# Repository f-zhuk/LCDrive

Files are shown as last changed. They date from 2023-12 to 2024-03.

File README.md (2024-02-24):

# LCDrive
This project shows what happens if you take an ordinary cycloidal reducer and unfold it into a straight line
Well, not so straight actually

The actuator is made out of four plates, two of which are guiding plates for alignment and two are pushing sliders.
In this device, sliders travel in circles with a radius of 1mm relative to the alignment plate. Sliders are 180 degrees out of phase.
Travel trajectory is defined by eccentrics mounted on shafts of two motors that run synchronously.
All plates have slots. Sliders have cycloidal cutouts, alignments have linear path cutouts. 

Now let’s add the carriage. All cutouts have a width equal to pin's diameter. The pin is ideally an integral part of the carriage and it engages with the edges of the cutouts. Cutouts in all plates define the exact position of the pin at every moment in time.

Pin and carriage respectively are pushed along the axis with the motors rotation.

In full-step mode, it takes 32 steps for one revolution of the internal shaft, 63.68 turns of the internal shaft for the single main shaft revolution, and 1.59 main shaft revolutions to slide the carriage from start to finish, or 3240 steps in total. 

In the ideal world, it is approximately 3.1 micrometers of linear movement per step.

Since I am not satisfied with current situation with parametric curves and offset tools in FreeCAD I wrote a small Python script to generate SVGs for import. Extruded pads I have prototyped with FDM which took me a couple of iterations. Then I milled my parts with a 1mm endmill out of 2mm aluminum strip. Using FreeCAD as a CAM has its drawbacks and at this point I think it might be reasonable to generate G-code in the same Python script skipping the FreeCAD part.

Advantages: 

1. No screw drive
2. Slim design
3. Great step distance

Disadvantages:

1. Large backlash
2. High resistance resulting in low pushing force

Possible improvements:

1. Add one more phase to get a 120-degree difference between moving slides
2. Add miniature bearings
3. Motor synchronization and feedback

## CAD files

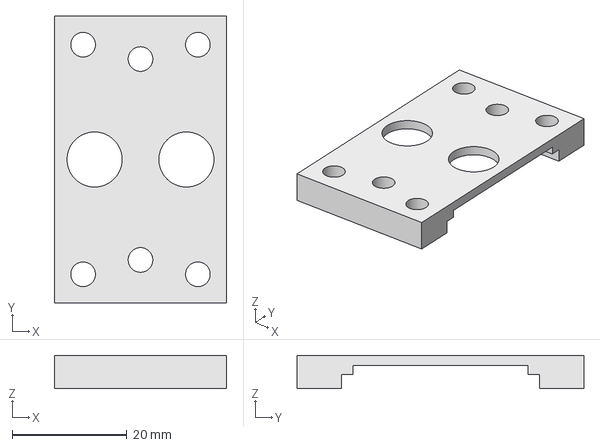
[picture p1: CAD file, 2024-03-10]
Mechanical/motor_top-motor_top.step
30.0 x 50.0 x 5.80 mm
LCS_0
motor_top001

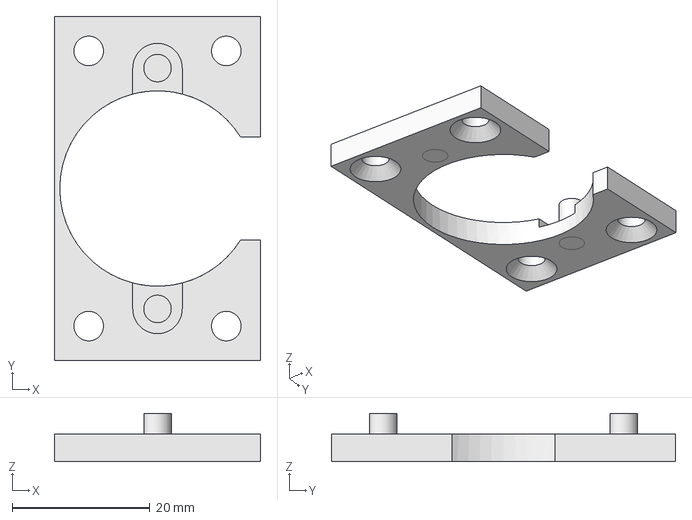
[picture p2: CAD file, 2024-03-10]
Mechanical/motor_bot-motor_bot.step
30.0 x 50.0 x 7.00 mm
LCS_0
motor_bot001

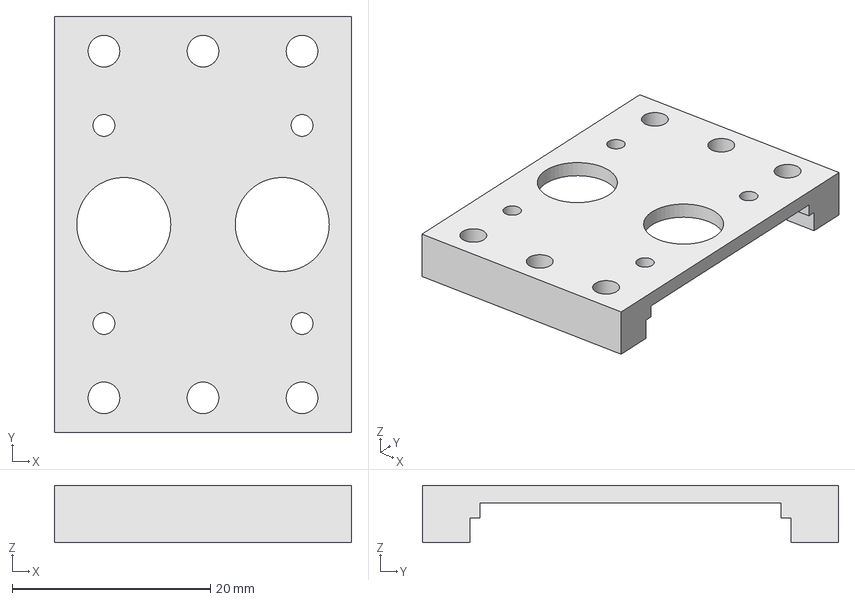
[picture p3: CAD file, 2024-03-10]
Mechanical/carriage_top-carriage_top.step
30.0 x 42.0 x 5.80 mm
LCS_0
carriage_top001

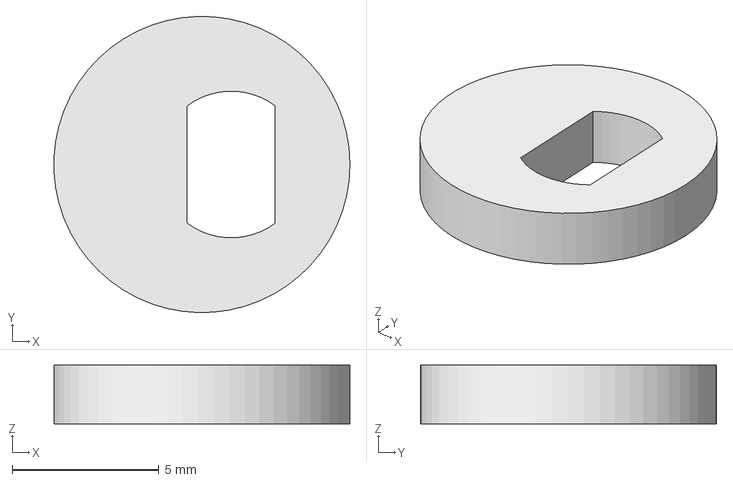
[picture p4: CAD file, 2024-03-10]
Mechanical/eccentric-eccentric.step
10.1 x 10.1 x 2.00 mm
LCS_0
eccentric001

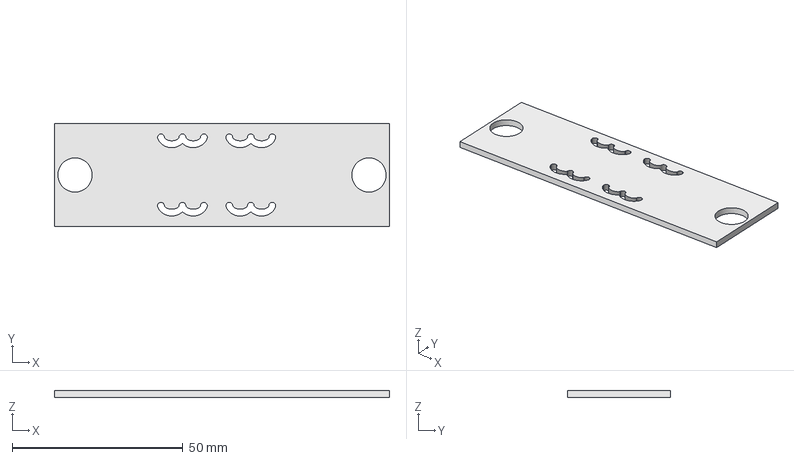
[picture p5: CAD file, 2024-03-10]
Mechanical/slot-slot.step
98.0 x 30.0 x 2.00 mm
LCS_0
slot001

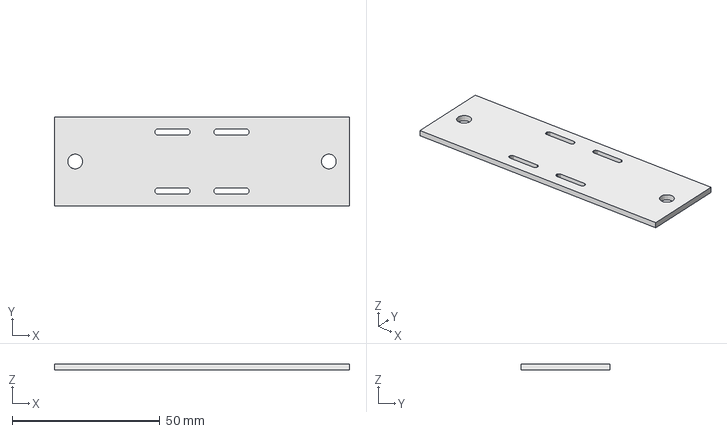
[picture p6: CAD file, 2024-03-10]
Mechanical/base-base.step
100.0 x 30.0 x 2.00 mm
LCS_0
base001

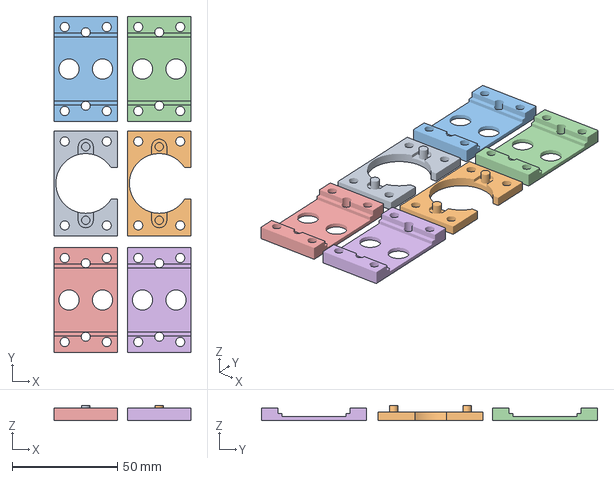
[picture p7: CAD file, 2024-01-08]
Mechanical/motor_case.3mf
65.0 x 160.0 x 7.00 mm
motor_bot-motor_bot.stl x 2
motor_top-motor_top.stl x 4

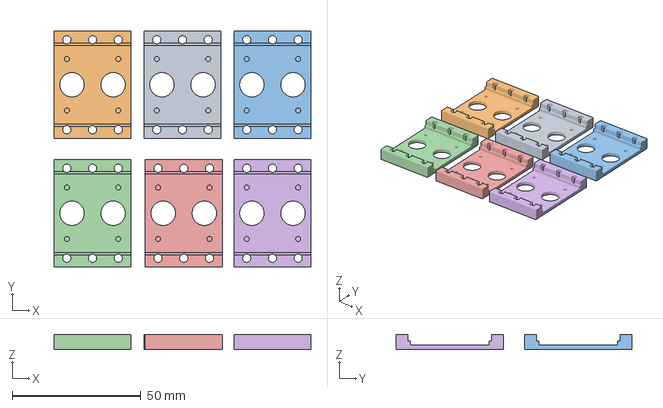
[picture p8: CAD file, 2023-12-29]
Mechanical/carriage_top-carriage_topcarriage_top001.3mf
100.0 x 92.0 x 5.80 mm
carriage_top-carriage_topcarriage_top001.stl x 6

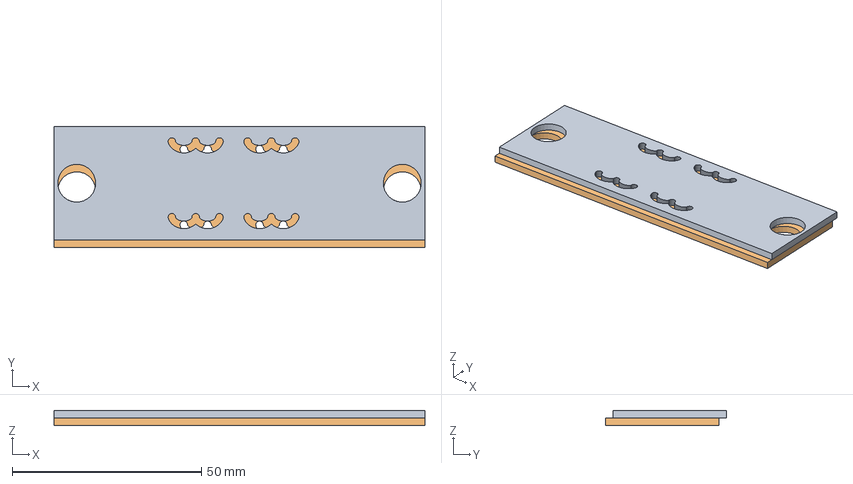
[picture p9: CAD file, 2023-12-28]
Mechanical/slot.FCStd
98.0 x 32.0 x 4.00 mm
slot001
slot002

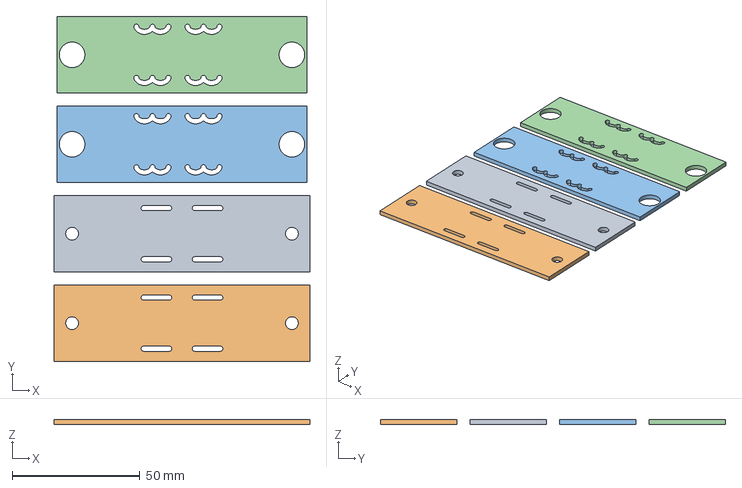
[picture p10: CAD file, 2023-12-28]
Mechanical/base-basebase001.3mf
100.0 x 135.0 x 2.00 mm
base-basebase001.stl x 2
slot-slotslot001.stl x 2

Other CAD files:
Mechanical/motor_top.FCStd
Mechanical/motor_bot.FCStd
Mechanical/eccentric.FCStd
Mechanical/slot_mill.FCStd
Mechanical/carriage_top.FCStd
Mechanical/base_mill.FCStd
Mechanical/slot-slotslot001.stl
Mechanical/base.FCStd
Mechanical/base-basebase001.stl
Mechanical/carriage_top-carriage_topcarriage_top001.stl
Mechanical/eccentric-eccentric.3mf
Mechanical/eccentric-eccentric.stl
Mechanical/motor_bot-motor_bot.stl
Mechanical/motor_top-motor_top.stl

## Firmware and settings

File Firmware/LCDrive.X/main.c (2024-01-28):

/**
  Generated Main Source File

  Company:
    Microchip Technology Inc.

  File Name:
    main.c

  Summary:
    This is the main file generated using PIC10 / PIC12 / PIC16 / PIC18 MCUs

  Description:
    This header file provides implementations for driver APIs for all modules selected in the GUI.
    Generation Information :
        Product Revision  :  PIC10 / PIC12 / PIC16 / PIC18 MCUs - 1.81.8
        Device            :  PIC18F26K83
        Driver Version    :  2.00
*/

/*
    (c) 2018 Microchip Technology Inc. and its subsidiaries. 
    
    Subject to your compliance with these terms, you may use Microchip software and any 
    derivatives exclusively with Microchip products. It is your responsibility to comply with third party 
    license terms applicable to your use of third party software (including open source software) that 
    may accompany Microchip software.
    
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
    IN NO EVENT WILL MICROCHIP BE LIABLE FOR ANY INDIRECT, SPECIAL, PUNITIVE, 
    INCIDENTAL OR CONSEQUENTIAL LOSS, DAMAGE, COST OR EXPENSE OF ANY KIND 
    WHATSOEVER RELATED TO THE SOFTWARE, HOWEVER CAUSED, EVEN IF MICROCHIP 
    HAS BEEN ADVISED OF THE POSSIBILITY OR THE DAMAGES ARE FORESEEABLE. TO 
    THE FULLEST EXTENT ALLOWED BY LAW, MICROCHIP'S TOTAL LIABILITY ON ALL 
    CLAIMS IN ANY WAY RELATED TO THIS SOFTWARE WILL NOT EXCEED THE AMOUNT 
    OF FEES, IF ANY, THAT YOU HAVE PAID DIRECTLY TO MICROCHIP FOR THIS 
    SOFTWARE.
*/

#include "mcc_generated_files/mcc.h"

void TMR0_stepISR()
{
    static uint16_t step = 0;
    step ++;
    if(step == 3500) 
    {
        DMA1CON1 = (DMA1CON1&~0x06)|0x04;
        DMA1SSA = (&SrcVarName0)+8;
    }
    if(step > 7000) 
    {
        step = 0;
        DMA1CON1 = (DMA1CON1&~0x06)|0x02;
        DMA1SSA = &SrcVarName0;
    }
}

/*
                         Main application
 */
void main(void)
{
    // Initialize the device
    SYSTEM_Initialize();
    
    TMR0_SetInterruptHandler (TMR0_stepISR);
    
    SrcVarName0[0] = 0x09;
    SrcVarName0[1] = 0x0C;
    SrcVarName0[2] = 0x06;
    SrcVarName0[3] = 0x03;
    SrcVarName0[4] = 0x09;
    SrcVarName0[5] = 0x0C;
    SrcVarName0[6] = 0x06;
    SrcVarName0[7] = 0x03;
    //SrcVarName0[0] = 0x09;
    //SrcVarName0[1] = 0x05;
    //SrcVarName0[2] = 0x06;
    //SrcVarName0[3] = 0x0A;
    //SrcVarName0[4] = 0x09;
    //SrcVarName0[5] = 0x05;
    //SrcVarName0[6] = 0x06;
    //SrcVarName0[7] = 0x0A;
    DMA1DSA= (volatile unsigned short)&PORTC; //DMA1 destination address

    // If using interrupts in PIC18 High/Low Priority Mode you need to enable the Global High and Low Interrupts
    // If using interrupts in PIC Mid-Range Compatibility Mode you need to enable the Global Interrupts
    // Use the following macros to:
    
    // Enable high priority global interrupts.
    INTERRUPT_GlobalInterruptHighEnable();

    // Enable low priority global interrupts.
    INTERRUPT_GlobalInterruptLowEnable();
    
    // Disable high priority global interrupts
    //INTERRUPT_GlobalInterruptHighDisable();

    // Disable low priority global interrupts.
    //INTERRUPT_GlobalInterruptLowDisable();

    while (1)
    {
        // Add your application code
    }
}
/**
 End of File
*/

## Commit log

2023-12-24 Initial push
    [eccentric-eccentricEccentric.3mf, eccentric-eccentricEccentric.stl, eccentric.FCStd]
2023-12-27 linear slot routine added
2023-12-28 Slice added
    [base-basebase001.3mf, base-basebase001.stl, base.FCStd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]
2023-12-28 pepositioned cycloidal slots
    [base-basebase001.3mf, slot-Body.stl, slot-slotslot001.stl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]
2023-12-28 Accidental save
    [eccentric.FCStd]
2023-12-28 carriage files added
    [carriage_top-carriage_topcarriage_top001.3mf, carriage_top-carriage_topcarriage_top001.stl, carriage_top.FCStd]
2023-12-28 ununtentional save
    [carriage_top.FCStd]
2023-12-29 opening enlarged
    [base_mill.FCStd, carriage_top-carriage_topcarriage_top001.3mf, carriage_top-carriage_topcarriage_top001.stl]
2023-12-29 through holes for pins added
    [carriage_top-carriage_topcarriage_top001.stl, carriage_top.FCStd]
2024-01-06 Post processed mill numerical control program for the slot part
    [slot_mill.FCStd]
2024-01-06 Eccentric split in two parts
    [eccentric-eccentric.3mf, eccentric-eccentric.stl, eccentric.FCStd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]
2024-01-08 Updated motor clamp design for M4
    [motor_bot-motor_bot.stl, motor_bot.FCStd, motor_case.3mf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]
2024-03-10 Deleted unused combined ecentric and tested step output
    [base-base.step, eccentric-eccentricEccentric.3mf, eccentric-eccentricEccentric.stl]
2024-03-10 Rest of STEPs added
    [carriage_top-carriage_top.step, eccentric-eccentric.step, motor_bot-motor_bot.step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]
